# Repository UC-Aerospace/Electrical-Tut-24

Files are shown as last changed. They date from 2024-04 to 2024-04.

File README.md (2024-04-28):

# 2024 Avionics tutorial example boards!!
Here's where you'll find basic examples of a flight computer board using the RP2040 microcontroller. 

We have two different example sizes.  
  
(50mm x 50mm) This shows it's possible to design a 2-layer 50mm x 50mm board to fit the minimum rocket tube diameter of 50mm. Made by Grayson. This is the one we have ordered and will be avalible to pass around.  
  
~~(66mm x 66mm) This 2-layer example board is slightly bigger but small enough to fit in an L2 rocket. Made by Kaden.~~  
Unfortunatly this board has some issues at the moment, we might look into fixing it. Left for now as it shows a different general approach.

> [!NOTE]
> While making a 2-layer 50mm x 50mm board is possible, routing something this small can be quite a puzzle especially to do nicely. If you do target 50x50 we would reccomend a 4-layer board. Otherwise, we'd suggest something either 66x66mm or 88x88mm.

> [!CAUTION]
> We are not experts and are still all learning a lot ourselves. As such some of these designs may be suboptimal, don't take them as best practice. If you see an issue with any of the boards, or even just think you do, feel free to create an issue so we can all learn.

## Templates

These are barebones files to use as a starting point, and very simply include a board outline with holes that will match with our sleds, the RP2040 footprint and the Sense module footprint. Avalible in 50x50, 66x66 and 88x88 to modify as you wish.

## Resources / Datasheets
**_Please look_** at the datasheets for any major components you plan to use, e.g. (Voltage regulator, RP2040, Flash chip, Screen, LEDs, USB-C connector, etc..) They provide the information necessary to integrate them with your project and if any extra components are needed to work correctly.

The Raspberry Pi Foundation has provided a massive amount of technical information for the RP2040 microcontroller we use, so I'd suggest reviewing their datasheets to help build your boards! They definitely helped me :) 

[RP2040 Datasheet](https://datasheets.raspberrypi.com/rp2040/rp2040-datasheet.pdf)  
[RP2040 Hardware design examples](https://datasheets.raspberrypi.com/rp2040/hardware-design-with-rp2040.pdf)  
[Raspberry Pi Pico datasheet](https://datasheets.raspberrypi.com/pico/pico-datasheet.pdf)
  
Also take a look at the sensor package used which we have got assembled for you:
[MicroSense](https://github.com/UC-Aerospace/Sense)

If you have any questions about the example board, then come talk to me!  
Happy making! (The first year Grayson) :3


  
^ Graysons demo flight computer, we will have a few to pass around.

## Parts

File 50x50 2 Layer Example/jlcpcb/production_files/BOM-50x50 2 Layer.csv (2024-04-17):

Comment | Designator | Footprint | LCSC
470R | R6 | R_0805_2012Metric_Pad1.20x1.40mm_HandSolder | C114564
LED | D6 | LED_0402_1005Metric_Pad0.77x0.64mm_HandSolder | C136118
360R | R11 | R_0805_2012Metric_Pad1.20x1.40mm_HandSolder | C137444
130 | R18,R19,R20 | R_0805_2012Metric_Pad1.20x1.40mm_HandSolder | C137474
Conn_01x03 | J4 | PinSocket_1x03_P2.54mm_Vertical | C146243
0.15A | F1 | Fuse_0603_1608Metric | C151137
Conn_01x02 | J1,SW1 | JST_XH_B2B-XH-A_1x02_P2.50mm_Vertical | C158012
10uF | C2,C7 | C_0805_2012Metric_Pad1.18x1.45mm_HandSolder | C15850
10k | R10,R8 | R_0805_2012Metric_Pad1.20x1.40mm_HandSolder | C17414
0R | R1 | R_0805_2012Metric_Pad1.20x1.40mm_HandSolder | C17477
1k | R2,R9 | R_0805_2012Metric_Pad1.20x1.40mm_HandSolder | C17513
27.4 | R12,R13 | R_0805_2012Metric_Pad1.20x1.40mm_HandSolder | C17588
20pF | C4,C5 | C_0805_2012Metric_Pad1.18x1.45mm_HandSolder | C1798
RP2040 | U1 | QFN-56-1EP_7x7mm_P0.4mm_EP3.2x3.2mm | C2040
Orange LED | D4 | LED_0603_1608Metric | C205445
LED | D7 | LED_0402_1005Metric_Pad0.77x0.64mm_HandSolder | C264408
5.1k | R5,R7 | R_0805_2012Metric_Pad1.20x1.40mm_HandSolder | C27834
100nF | C1,C11,C12,C13,C14,C15,C3,C6,C8,C9 | C_0805_2012Metric_Pad1.18x1.45mm_HandSolder | C28233
1uF | C10,C16 | C_0805_2012Metric_Pad1.18x1.45mm_HandSolder | C28323
Reset | SW2 | SW_SPST_PTS645 | C2837531
D_Schottky | D1,D2 | D_SMA | C2909963
USB_C_Receptacle_USB2.0_14P | J3 | USB_C_Receptacle_GCT_USB4105-xx-A_16P_TopMnt_Horizontal | C2988369
5.6k | R4 | R_0805_2012Metric_Pad1.20x1.40mm_HandSolder | C4382
Conn_01x02 | J2 | PinHeader_1x02_P2.54mm_Vertical | C49661
12MHz | Y1 | Crystal_SMD_3225-4Pin_3.2x2.5mm_HandSoldering | C50430
Conn_01x04 | J5 | PinSocket_1x04_P2.54mm_Vertical | C5116483
4K7 | R14,R15,R16,R17 | R_0805_2012Metric_Pad1.20x1.40mm_HandSolder | C60816
Voltage Regulator | U3 | SOT-223 | C6186
D_Zener | D3 | D_SOD-123 | C668891
LED | D8 | LED_0402_1005Metric_Pad0.77x0.64mm_HandSolder | C74339
Green LED | D5 | LED_0603_1608Metric | C84264
W25Q128JVPIQ TR | U2 | SOIC-8_5.23x5.23mm_P1.27mm | C97521

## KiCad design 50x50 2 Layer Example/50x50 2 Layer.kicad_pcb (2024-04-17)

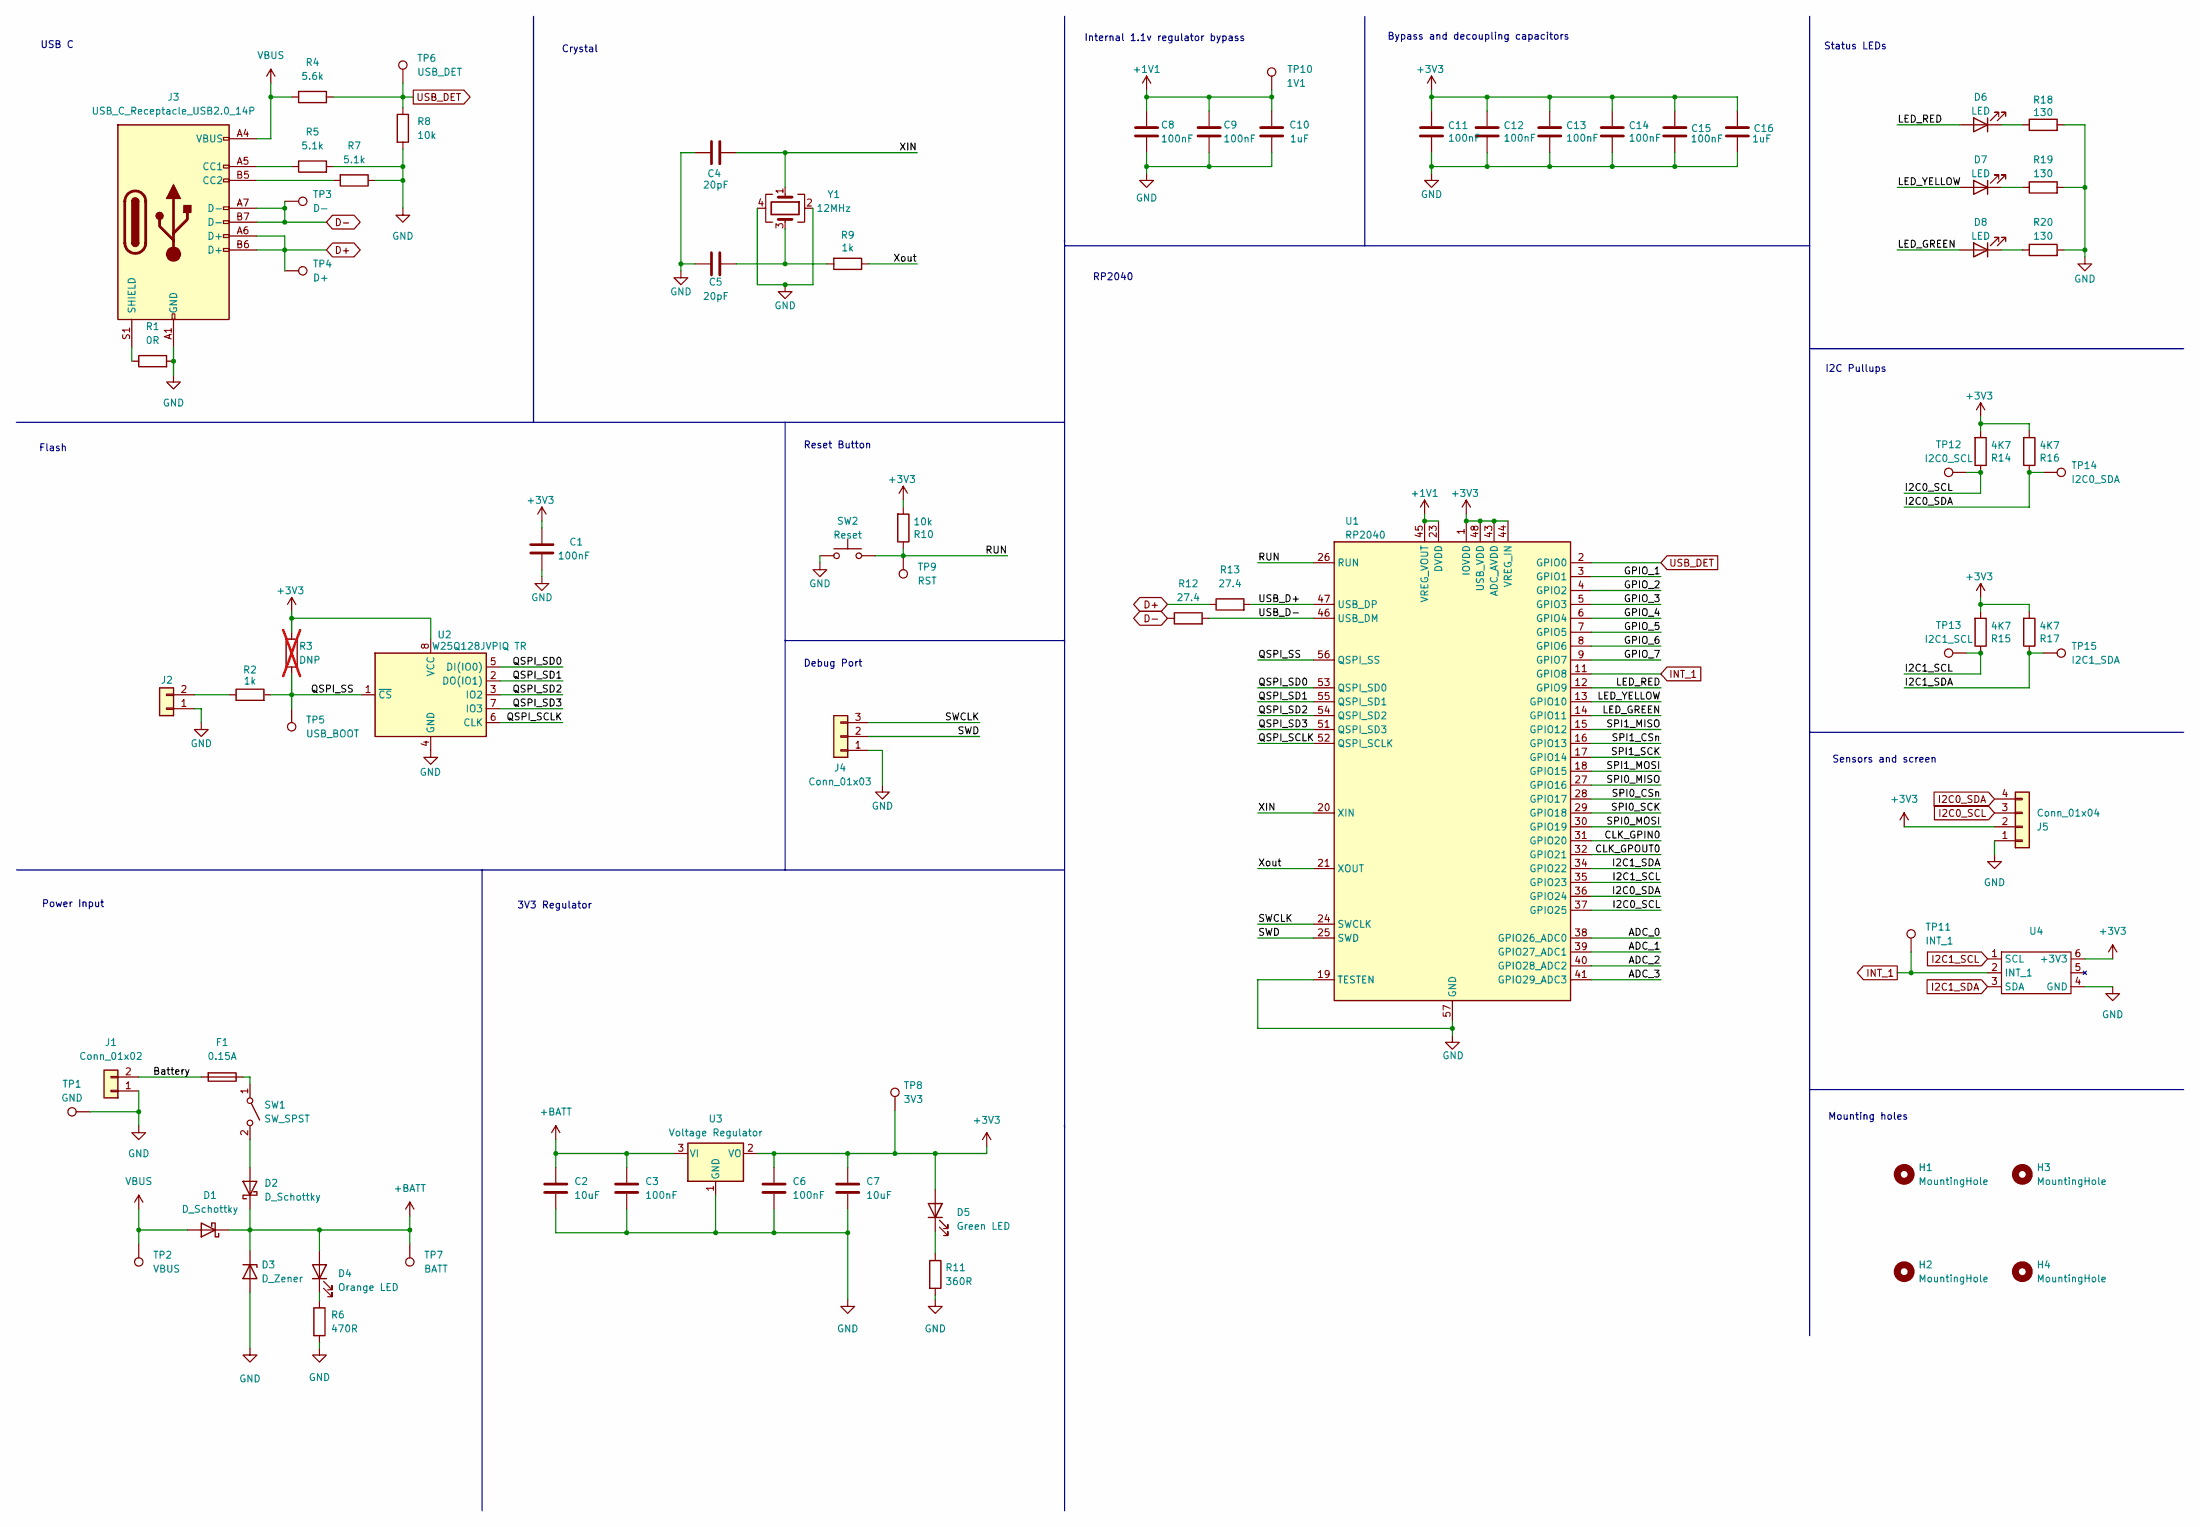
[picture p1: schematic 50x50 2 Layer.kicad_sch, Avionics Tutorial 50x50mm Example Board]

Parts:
C1, C8, C9, C11, C12, C13, C14: 100nF; C_0805_2012Metric_Pad1.18x1.45mm_HandSolder; MPN CL10B104KB8NNWC
C2, C7: 10uF; C_0805_2012Metric_Pad1.18x1.45mm_HandSolder; MPN CL21A106KOQNNNE
C3, C6: 100nF; C_0805_2012Metric_Pad1.18x1.45mm_HandSolder; MPN CL21B104KBCNNNC
C4, C5: 20pF; C_0805_2012Metric_Pad1.18x1.45mm_HandSolder; MPN 0603N270J500CT
C10, C16: 1uF; C_0805_2012Metric_Pad1.18x1.45mm_HandSolder; MPN CL10B105KA8NNNC
C15: 100nF; C_0805_2012Metric_Pad1.18x1.45mm_HandSolder; MPN CL10B105KA8NNNC
D1, D2: D_Schottky; D_SMA; MPN 4786-SK34ACT-ND
D3: D_Zener; D_SOD-123; MPN BZT52C12-TP
D4: Orange LED; LED_0603_1608Metric; MPN B1911UD--20D001014U1930
D5: Green LED; LED_0603_1608Metric; MPN B1931NG--20D001114U1930
D6: LED; LED_0402_1005Metric_Pad0.77x0.64mm_HandSolder; MPN 150040RS73240
D7: LED; LED_0402_1005Metric_Pad0.77x0.64mm_HandSolder; MPN 150040YS73240
D8: LED; LED_0402_1005Metric_Pad0.77x0.64mm_HandSolder; MPN 150040VS73240
F1: 0.15A; Fuse_0603_1608Metric; MPN FMC16302WHTP
H1, H2, H3, H4: MountingHole; MountingHole_3.2mm_M3
J1: Conn_01x02; JST_XH_B2B-XH-A_1x02_P2.50mm_Vertical; MPN S2B-XH-A(LF)(SN)
J2: Conn_01x02; PinHeader_1x02_P2.54mm_Vertical
J3: USB_C_Receptacle_USB2.0_14P; USB_C_Receptacle_GCT_USB4105-xx-A_16P_TopMnt_Horizontal
J4: Conn_01x03; PinSocket_1x03_P2.54mm_Vertical
J5: Conn_01x04; PinSocket_1x04_P2.54mm_Vertical
R1: 0R; R_0805_2012Metric_Pad1.20x1.40mm_HandSolder
R2, R9: 1k; R_0805_2012Metric_Pad1.20x1.40mm_HandSolder; MPN RMCF0603FT1K00
R3: DNP; R_0805_2012Metric_Pad1.20x1.40mm_HandSolder; not fitted
R4: 5.6k; R_0805_2012Metric_Pad1.20x1.40mm_HandSolder
R5, R7: 5.1k; R_0805_2012Metric_Pad1.20x1.40mm_HandSolder
R6: 470R; R_0805_2012Metric_Pad1.20x1.40mm_HandSolder; MPN RC0805JR-07360RL
R8: 10k; R_0805_2012Metric_Pad1.20x1.40mm_HandSolder
R10: 10k; R_0805_2012Metric_Pad1.20x1.40mm_HandSolder; MPN RMCF0603FT10K0
R11: 360R; R_0805_2012Metric_Pad1.20x1.40mm_HandSolder; MPN RC0805JR-07360RL
R12, R13: 27.4; R_0805_2012Metric_Pad1.20x1.40mm_HandSolder
R14, R15, R16, R17: 4K7; R_0805_2012Metric_Pad1.20x1.40mm_HandSolder; MPN RC0603FR-074K7L
R18, R19, R20: 130; R_0805_2012Metric_Pad1.20x1.40mm_HandSolder; MPN RC0603FR-07130RL
SW1: SW_SPST; JST_XH_B2B-XH-A_1x02_P2.50mm_Vertical; MPN S2B-XH-A(LF)(SN)
SW2: Reset; SW_SPST_PTS645; MPN PTS645SM43SMTR92 LFS
TP1: GND; TestPoint_Pad_1.0x1.0mm; MPN S1751-46R
TP2: VBUS; TestPoint_Pad_1.0x1.0mm; MPN S1751-46R
TP3: D-; TestPoint_Pad_1.0x1.0mm; MPN S1751-46R
TP4: D+; TestPoint_Pad_1.0x1.0mm; MPN S1751-46R
TP5: USB_BOOT; TestPoint_Pad_1.0x1.0mm; MPN S1751-46R
TP6: USB_DET; TestPoint_Pad_1.0x1.0mm; MPN S1751-46R
TP7: BATT; TestPoint_Pad_1.0x1.0mm; MPN S1751-46R
TP8: 3V3; TestPoint_Pad_1.0x1.0mm; MPN S1751-46R
TP9: RST; TestPoint_Pad_1.0x1.0mm; MPN S1751-46R
TP10: 1V1; TestPoint_Pad_1.0x1.0mm; MPN S1751-46R
TP11: INT_1; TestPoint_Pad_1.0x1.0mm; MPN S1751-46R
TP12: I2C0_SCL; TestPoint_Pad_1.0x1.0mm; MPN S1751-46R
TP13: I2C1_SCL; TestPoint_Pad_1.0x1.0mm; MPN S1751-46R
TP14: I2C0_SDA; TestPoint_Pad_1.0x1.0mm; MPN S1751-46R
TP15: I2C1_SDA; TestPoint_Pad_1.0x1.0mm; MPN S1751-46R
U1: RP2040; QFN-56-1EP_7x7mm_P0.4mm_EP3.2x3.2mm; MPN SC0914(13)
U2: W25Q128JVPIQ TR; SOIC-8_5.23x5.23mm_P1.27mm; MPN W25Q128JVPIQ TR
U3: Voltage Regulator; SOT-223; MPN BA033CC0FP-E2
U4: UCA_Sense
Y1: 12MHz; Crystal_SMD_3225-4Pin_3.2x2.5mm_HandSoldering

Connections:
+1V1: C8.1, C9.1, C10.2, TP10.1, U1.23 (DVDD), U1.45 (VREG_VOUT), U1.50 (DVDD)
+3V3: C1.2, C6.1, C7.1, C11.1, C12.1, C13.1, C14.1, C15.2, C16.2, D5.2 (A), J5.2, R3.1, R10.2, R14.2, R15.2, R16.2, R17.2, TP8.1, U1.1 (IOVDD), U1.10 (IOVDD), U1.22 (IOVDD), U1.33 (IOVDD), U1.42 (IOVDD), U1.43 (ADC_AVDD), U1.44 (VREG_IN), U1.48 (USB_VDD), U1.49 (IOVDD), U2.8 (VCC), U3.2 (VO), U4.6 (+3V3)
+BATT: C2.1, C3.1, D1.1 (K), D2.1 (K), D3.1 (K), D4.2 (A), TP7.1, U3.3 (VI)
/ADC_0: U1.38 (GPIO26_ADC0)
/ADC_1: U1.39 (GPIO27_ADC1)
/ADC_2: U1.40 (GPIO28_ADC2)
/ADC_3: U1.41 (GPIO29_ADC3)
/Battery: F1.2, J1.2
/CLK_GPIN0: U1.31 (GPIO20)
/CLK_GPOUT0: U1.32 (GPIO21)
/GPIO_1: U1.3 (GPIO1)
/GPIO_2: U1.4 (GPIO2)
/GPIO_3: U1.5 (GPIO3)
/GPIO_4: U1.6 (GPIO4)
/GPIO_5: U1.7 (GPIO5)
/GPIO_6: U1.8 (GPIO6)
/GPIO_7: U1.9 (GPIO7)
/LED_GREEN: D8.2 (A), U1.14 (GPIO11)
/LED_RED: D6.2 (A), U1.12 (GPIO9)
/LED_YELLOW: D7.2 (A), U1.13 (GPIO10)
/QSPI_SCLK: U1.52 (QSPI_SCLK), U2.6 (CLK)
/QSPI_SD0: U1.53 (QSPI_SD0), U2.5 (DI(IO0))
/QSPI_SD1: U1.55 (QSPI_SD1), U2.2 (DO(IO1))
/QSPI_SD2: U1.54 (QSPI_SD2), U2.3 (IO2)
/QSPI_SD3: U1.51 (QSPI_SD3), U2.7 (IO3)
/QSPI_SS: R2.2, R3.2, TP5.1, U1.56 (QSPI_SS), U2.1 (~CS)
/RUN: R10.1, SW2.2, TP9.1, U1.26 (RUN)
/SPI0_CSn: U1.28 (GPIO17)
/SPI0_MISO: U1.27 (GPIO16)
/SPI0_MOSI: U1.30 (GPIO19)
/SPI0_SCK: U1.29 (GPIO18)
/SPI1_CSn: U1.16 (GPIO13)
/SPI1_MISO: U1.15 (GPIO12)
/SPI1_MOSI: U1.18 (GPIO15)
/SPI1_SCK: U1.17 (GPIO14)
/SWCLK: J4.3, U1.24 (SWCLK)
/SWD: J4.2, U1.25 (SWD)
/USB_D+: R13.2, U1.47 (USB_DP)
/USB_D-: R12.2, U1.46 (USB_DM)
/XIN: C4.1, U1.20 (XIN), Y1.1
/Xout: R9.1, U1.21 (XOUT)
D+: J3.A6 (D+), J3.B6 (D+), R13.1, TP4.1
D-: J3.A7 (D-), J3.B7 (D-), R12.1, TP3.1
GND: C1.1, C2.2, C3.2, C4.2, C5.2, C6.2, C7.2, C8.2, C9.2, C10.1, C11.2, C12.2, C13.2, C14.2, C15.1, C16.1, D3.2 (A), J1.1, J2.1, J3.A1 (GND), J3.A12 (GND), J3.B1 (GND), J3.B12 (GND), J4.1, J5.1, R1.2, R5.2, R6.2, R7.1, R8.2, R11.2, R18.2, R19.2, R20.2, SW2.1, TP1.1, U1.19 (TESTEN), U1.57 (GND), U2.4 (GND), U3.1 (GND), U4.4 (GND), Y1.2, Y1.4
I2C0_SCL: J5.3, R14.1, TP12.1, U1.37 (GPIO25)
I2C0_SDA: J5.4, R16.1, TP14.1, U1.36 (GPIO24)
I2C1_SCL: R15.1, TP13.1, U1.35 (GPIO23), U4.1 (SCL)
I2C1_SDA: R17.1, TP15.1, U1.34 (GPIO22), U4.3 (SDA)
INT_1: TP11.1, U1.11 (GPIO8), U4.2 (INT_1)
unnamed: C5.1, R9.2, Y1.3
unnamed: D2.2 (A), SW1.2 (B)
unnamed: D4.1 (K), R6.1
unnamed: D5.1 (K), R11.1
unnamed: D6.1 (K), R18.1
unnamed: D7.1 (K), R19.1
unnamed: D8.1 (K), R20.1
unnamed: J2.2, R2.1
unnamed: J3.A5 (CC1), R5.1
unnamed: J3.B5 (CC2), R7.2
unnamed: J3.S1 (SHIELD), R1.1
unnamed: F1.1, SW1.1 (A)
USB_DET: R4.2, R8.1, TP6.1, U1.2 (GPIO0)
VBUS: D1.2 (A), J3.A4 (VBUS), J3.A9 (VBUS), J3.B4 (VBUS), J3.B9 (VBUS), R4.1, TP2.1

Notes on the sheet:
Sensors and screen
Debug Port
Mounting holes
Power Input
Crystal
I2C Pullups
Internal 1.1v regulator bypass
RP2040
3V3 Regulator
Flash
USB C
Status LEDs
Reset Button
Bypass and decoupling capacitors

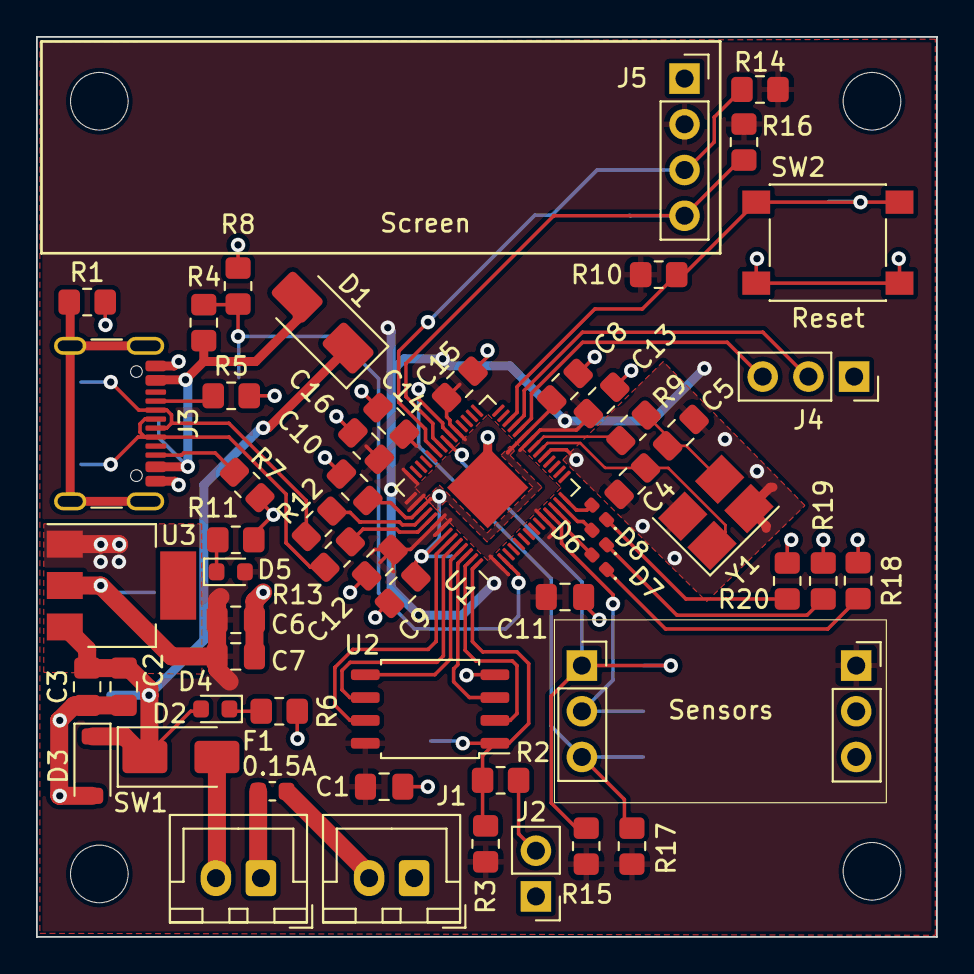
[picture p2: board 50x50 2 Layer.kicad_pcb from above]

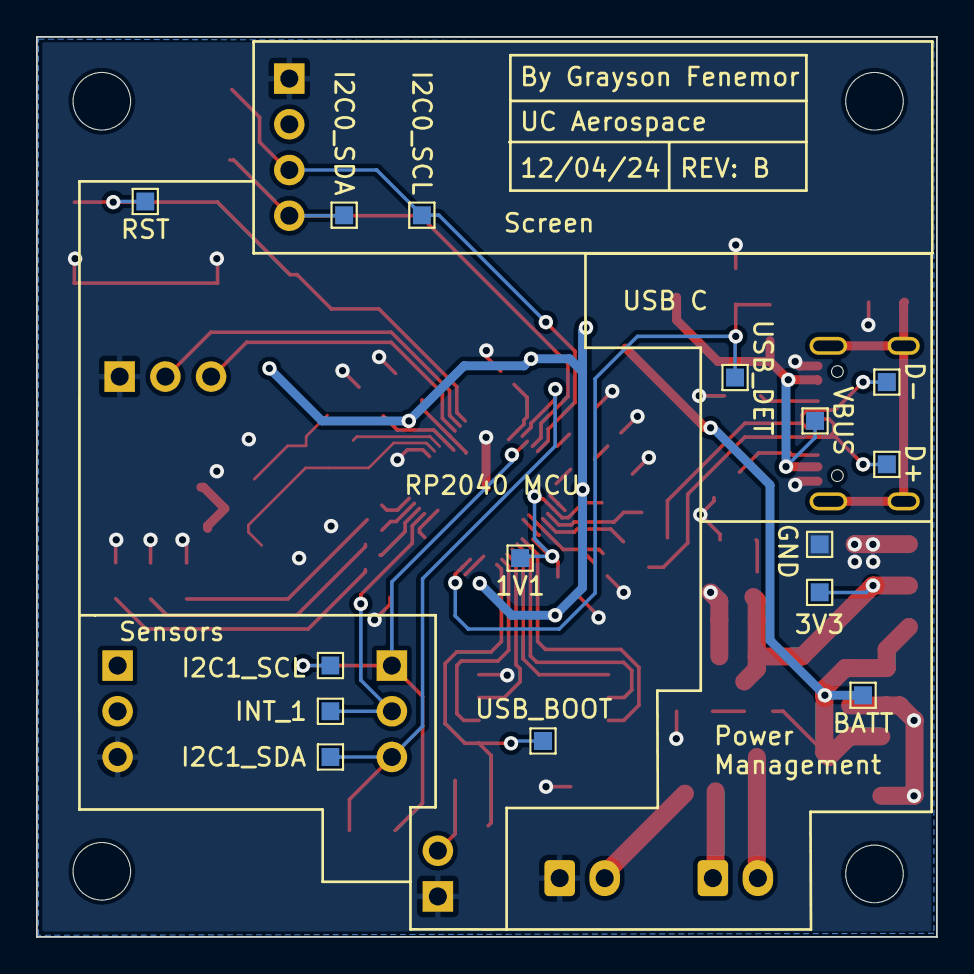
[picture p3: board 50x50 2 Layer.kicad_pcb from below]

Board: 2 copper layers, 50.0 x 50.0 mm, 76 parts (15 on the bottom side), 42 nets.

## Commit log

2024-04-03 Relocated the example
    [50x50 2 Layer.kicad_pcb, 50x50 2 Layer.kicad_sch]
2024-04-10 Updated Schematic
    [50x50 2 Layer.kicad_sch]
2024-04-11 Added 66x66 Board
    [66x66 2 Layer Example.kicad_pcb, 66x66 2 Layer Example.kicad_sch]
2024-04-11 Added sense footprint
2024-04-12 Updated 66x66 to fix Clarence issues. Minimum 0.2mm
    [66x66 2 Layer Example.kicad_pcb]
2024-04-12 Updated board and schematic
    PCB and schematic have been updated to REV B
    [50x50 2 Layer.kicad_pcb, 50x50 2 Layer.kicad_sch]
2024-04-12 Added 3D model for sense
    [50x50 2 Layer.kicad_pcb]
2024-04-12 Fixed screen connector and tidied GND plane
    The OLED screen connector was flipped, so fixed that. Tidied up some long GND paths as well.
    [50x50 2 Layer.kicad_pcb, 50x50 2 Layer.kicad_sch]
2024-04-17 Created BOM with LCSC components Linked BOM to Schematic Generated Production Files for JLCPCB
    [50x50 2 Layer-CuBottom.gbr, 50x50 2 Layer-CuTop.gbr, 50x50 2 Layer-EdgeCuts.gbr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]
2024-04-28 Added template boards
    [50x50.kicad_pcb, 50x50.kicad_sch, 66x66.kicad_pcb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]
2024-05-11 Updated Template, to give more of an Outline
    [50x50.kicad_sch, 66x66.kicad_sch, 88x88.kicad_sch]
2024-05-11 To be reviewed
    [After tutorial examples.kicad_pcb, After tutorial examples.kicad_sch]
2024-05-11 Nuke 66x66 2 Layer Example
    Several critical issues have rendered this one more of a hinderance than its worth. If you've referenced this design please carefully check that your Sense and screen footprints align with the other example.
    [66x66 2 Layer Example.kicad_pcb, 66x66 2 Layer Example.kicad_sch]
